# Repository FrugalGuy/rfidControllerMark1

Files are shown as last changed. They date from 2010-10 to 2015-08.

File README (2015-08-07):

This is the first incarnation of an Arduino-based RFID controller for an electric door strike.
This version does not do data logging or refer to an off-controller database for access control information.
Instead, RFID cards are registered directly at the reader.

  The sketch implements a controller for an RFID door lock system.
  It reads RFID cards and sends a signal to unlock a 
  door if the presented card is a valid card stored in EEPROM.
        
  The script currently can interface with HID card readers using Wiegand26
  protocol or with Innovations' ID-12 or ID-20 readers configured for 
  serial ASCII protocol.  The latter reads 125 KHz RFID cards / keyfobs.
   
  Additional features:
  1) System begins in 'factory default' mode. This is a 'virgin'
     state with no stored cards. When in this mode, lights flash in 
     a frenetic way. The first RFID card read after installation
     will become the 'master card' and factory default mode is exited.
     This little feature means you can burn tons of these chips and
     you don't need to hard-code any RFIDs. Suitable for shipping!
       
  2) Master card (first card read after installation) also opens
     the door, so you can just use that card for every day access
     instead of having to stash it somewhere.
        
  3) You can enter programming mode at any time with the Master card.
     To do this, you swipe the master card twice within a few seconds.
     First time opens the door, and second time (if door is still 
     unlocked) puts you in programming mode. You get sequential flashing 
     lights to indicate you are in programming mode.
    
  4) While in programming mode you can add any number of additional
     cards to the EEPROM. You can also remove any number of 
     cards from EEPROM while in this mode. You get a blinking green for
     adds and a blinking red for deletes. Previously unauthorized cards 
     will be added and authorized cards will be deleted. You exit 
     programming mode by swiping the master card again or after a period
     of inactivity.
			    
  5) Master card and other cards get a green/red light indicating
     pass/fail when trying to open the door.

  OPTIONAL FEATURES
  1) Master Swap option allows you to change the Master without
     resetting to factory default mode and erasing the additional
     cards. This is useful if you lose the Master card. Hold optional
     controller reset button for around 5 seconds.
  2) Device can be returned to factory default mode by pressing the 
     optional reset button for 15 seconds.
  3) Stealth option (not implemented) allows you to add your own RFID 
     card to the controller without having the Master card. Warning: Evil
			      
  DEVELOPMENT FEATURES
  1) Define a debug flag to get serial debug output.

  FUTURE POSSIBILITIES
  Data logging via wireless or HDSD card or enet/USB connector.
  Command line over serial to query and edit RFID database.
  IP web service interface for querying remote RFID db.
								      
  HARDWARE CONFIGURATIONS
  * Homegrown DIY using ID-12 or ID-20 RFID Reader
    I suggest two PCBs, one for the RFID reader and indicator lights 
    outside the door and a second for the controller inside. 
    Connect reader serial and light control lines to controller 
    located in a secure location (inside the access-controlled area). 
    Power for the door lock should be routed securely from the
    controller board to the door lock to prevent jumping. If you
    are providing a factory reset switch, some means of access to 
    the switch needs to be provided.
  * ProxPoint Plus Proximity Reader with Wiegand Output Model 6005
    For this you just need the interior controller connected to
    the reader outside the door, and power from the controller to
    the door lock.

  I've included Eagle files for the controller board and 
  Eagle files for the reader board for the ID-12/ID-20 chip
  configured for ASCII protocol.  You won't need the reader
  board if you're using a purchased HID Wiegand reader.

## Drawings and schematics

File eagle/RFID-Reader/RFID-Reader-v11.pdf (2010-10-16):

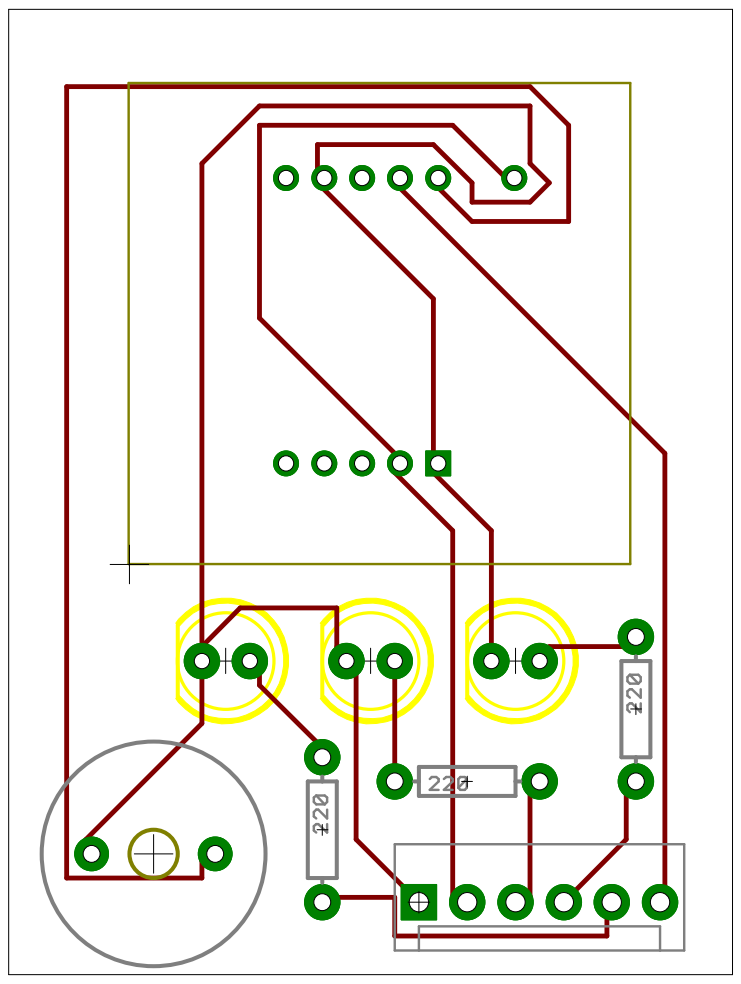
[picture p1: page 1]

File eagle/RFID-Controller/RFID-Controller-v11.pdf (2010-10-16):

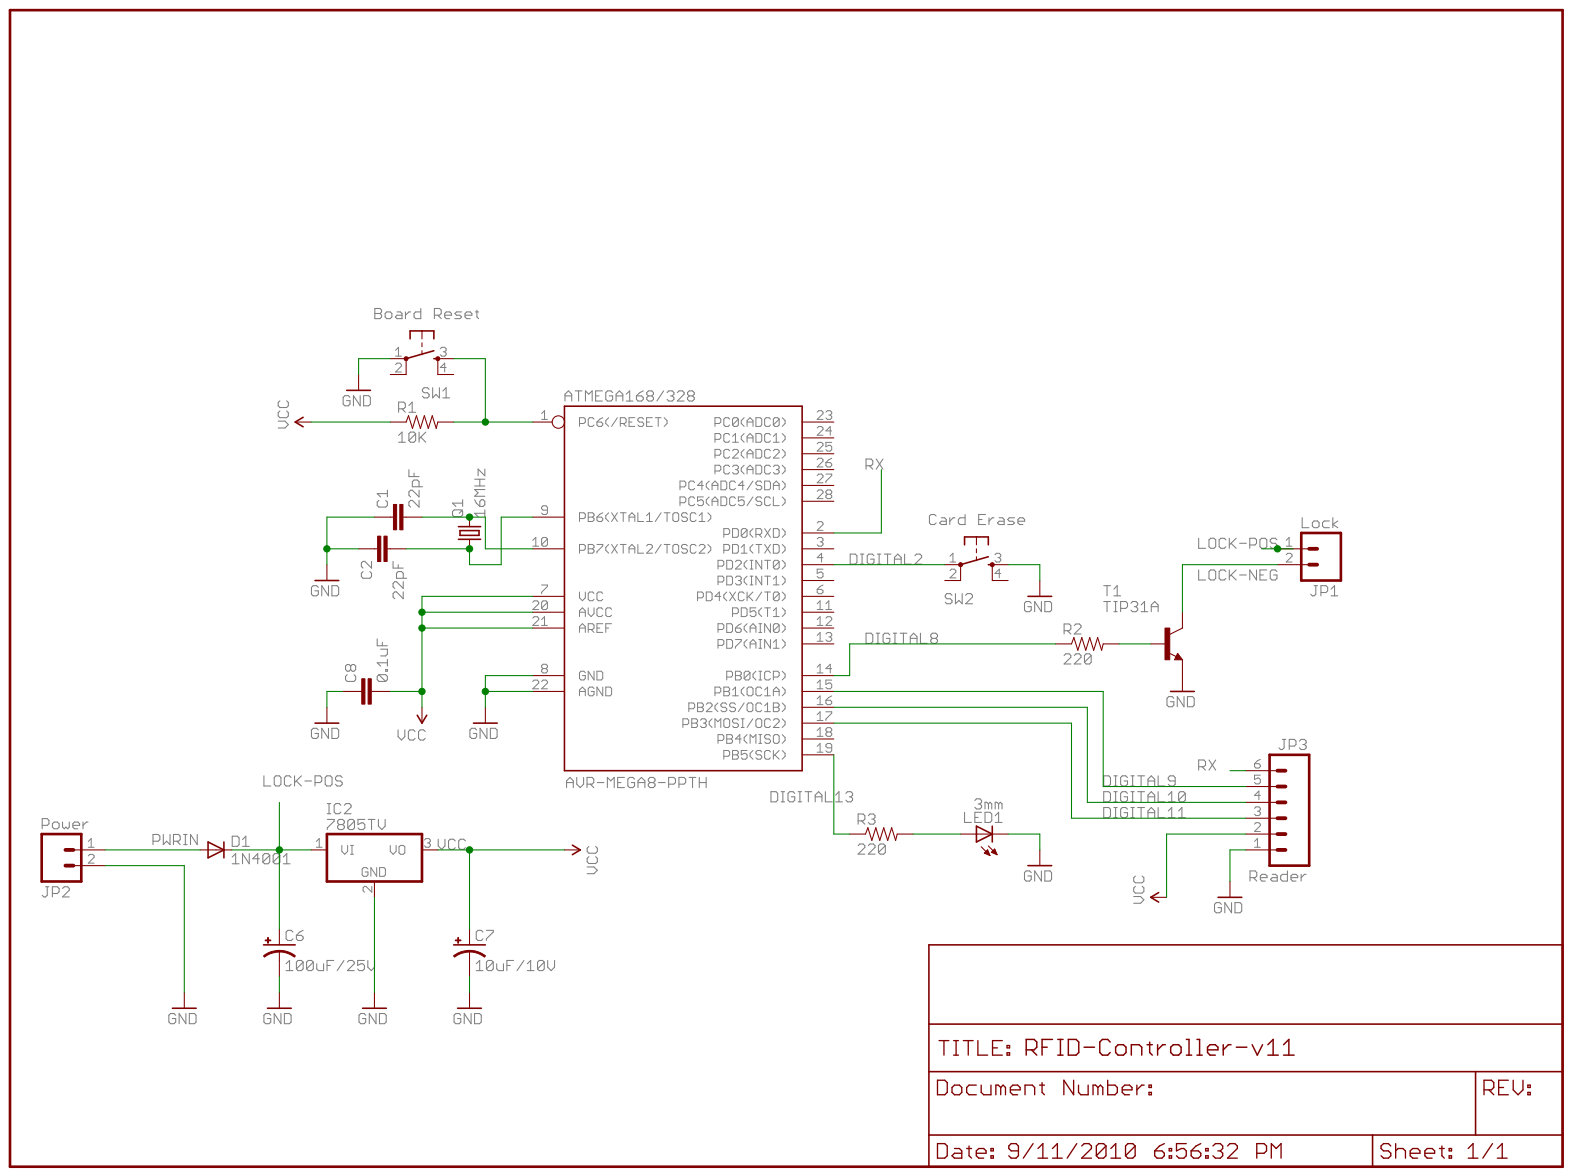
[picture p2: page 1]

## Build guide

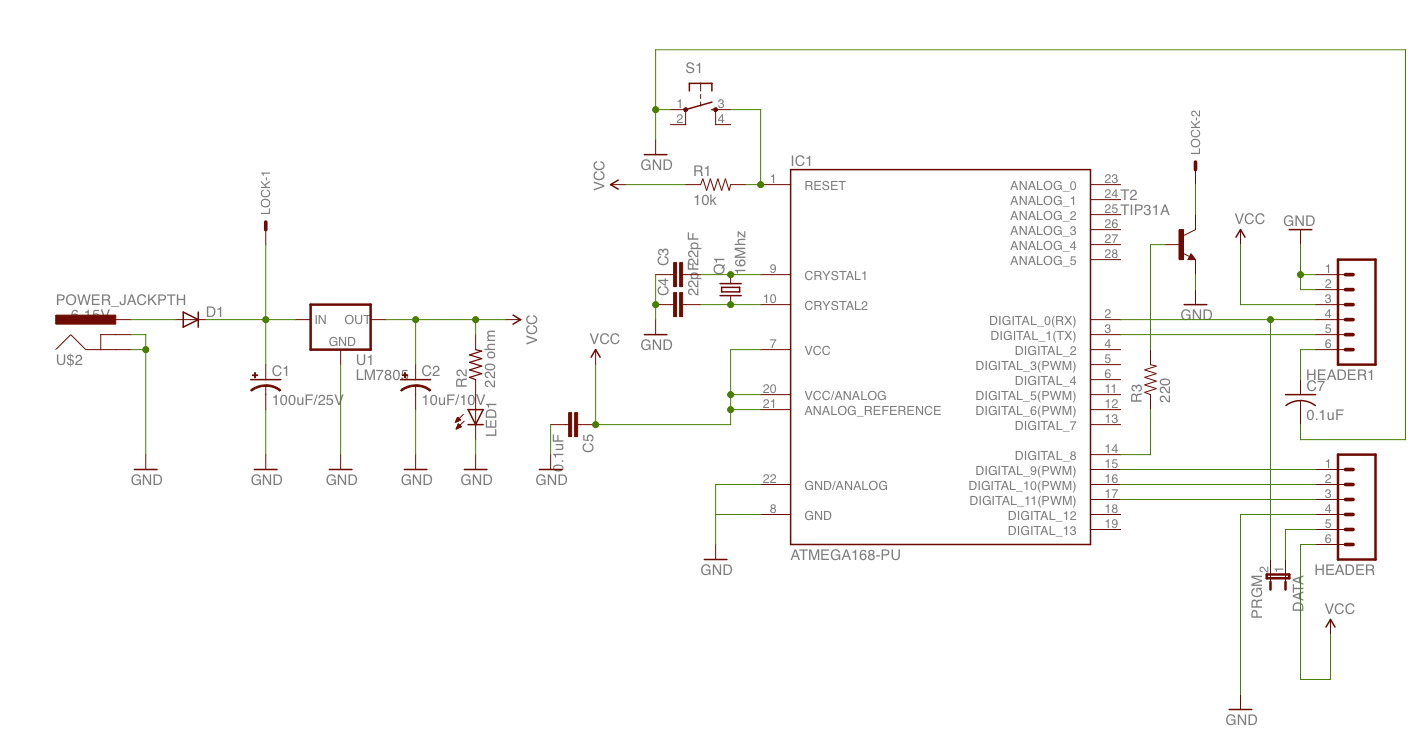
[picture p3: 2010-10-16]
eagle/RFID-Controller/Instructables-Schematic.png

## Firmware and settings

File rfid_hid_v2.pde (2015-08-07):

/*
  RFID Door Lock
  10APR2010, 17Oct2010
  Ron Craig
  roncraig007@gmail.com
  
  This sketch implements a controller for an RFID door lock system.
  It reads RFID cards and sends a signal to unlock a 
  door if the presented card is a valid card stored in EEPROM.
  
  The script currently can interface with HID card readers using Wiegand26
  protocol or with Innovations' ID-12 or ID-20 readers configured for 
  serial ASCII protocol.  The latter reads 125 KHz RFID cards / keyfobs.
  
  Additional features:
  1) System begins in 'factory default' mode. This is a 'virgin'
  state with no stored cards. When in this mode, lights flash in 
  a frenetic way. The first RFID card read after installation
  will become the 'master card' and factory default mode is exited.
  This little feature means you can burn tons of these chips and
  you don't need to hard-code any RFIDs. Suitable for shipping!
  
  2) Master card (first card read after installation) also opens
  the door, so you can just use that card for every day access
  instead of having to stash it somewhere.
  
  3) You can enter programming mode at any time with the Master card.
  To do this, you swipe the master card twice within a few seconds.
  First time opens the door, and second time (if door is still 
  unlocked) puts you in programming mode. You get sequential flashing 
  lights to indicate you are in programming mode.
  
  4) While in programming mode you can add any number of additional
  cards to the EEPROM. You can also remove any number of 
  cards from EEPROM while in this mode. You get a blinking green for
  adds and a blinking red for deletes. Previously unauthorized cards 
  will be added and authorized cards will be deleted. You exit 
  programming mode by swiping the master card again or after a period
  of inactivity.
  
  5) Master card and other cards get a green/red light indicating
  pass/fail when trying to open the door.
  
  OPTIONAL FEATURES
  1) Master Swap option allows you to change the Master without
  resetting to factory default mode and erasing the additional
  cards. This is useful if you lose the Master card. Hold optional
  controller reset button for around 5 seconds.
  2) Device can be returned to factory default mode by pressing the 
  optional reset button for 15 seconds.
  2) Stealth option (not implemented) allows you to add your own RFID 
  card to the controller without having the Master card. Warning: Evil
  
  DEVELOPMENT FEATURES
  1) Define a debug flag to get serial debug output.
  
  FUTURE POSSIBILITIES
  Data logging via wireless or HDSD card or enet/USB connector.
  Command line over serial to query and edit RFID database.
  IP web service interface for querying remote RFID db.
  
  HARDWARE CONFIGURATIONS
  * Homegrown DIY using ID-12 or ID-20 RFID Reader
  I suggest two PCBs, one for the RFID reader and indicator lights 
  outside the door and a second for the controller inside. 
  Connect reader serial and light control lines to controller 
  located in a secure location (inside the access-controlled area). 
  Power for the door lock should be routed securely from the
  controller board to the door lock to prevent jumping. If you
  are providing a factory reset switch, some means of access to 
  the switch needs to be provided.
  * ProxPoint Plus Proximity Reader with Wiegand Output Model 6005
  For this you just need the interior controller connected to
  the reader outside the door, and power from the controller to
  the door lock.

  
  COMPONENTS
  Mini SPST Push Button momentary reset switch (COM-00097 $0.35)
  
  ID-12/ID-20 RFID reader (SEN-08419 $29.95/SEN-08628 $34.95)

  Using www.sparkfun.com breakout board (SEN-08423 $0.95)
  [1] GND (Ground)
  [2] /RST (Reset Reader) Connect to +5V     
  [3] ANT (NC)  
  [4] ANT (NC)      
  [5] CP  (NC) (Card Present)     
  [6] NC
  [7] FS (Format select) (ground this for ASCII)
  [8] D1 (NC)
  [9] D0 (TTL Serial) to Arduino RX Pin
  [10] Buzzer/LED (Card read indicator) (Connect to transistor + buzzer/led to indicate card was read)
  [11] 5v+ ( +5vDC power) 

  On Arduino....
  [4] (Digital IN) to tactile push button reset switch connected to GND (optional)
  [13] (Digital OUT) to LED to indicate reset status (optional)
  [8] (Digital OUT) to lock relay+ 
  [9] (Digital OUT) to Red LED+ (fail/RFID erase indicator)
  [10] (Digital OUT) to Blue or Yellow LED+ (power indicator)
  [11] (Digital OUT) to Green LED+ (pass/RFID add indicator)
  [RX0] (Serial IN) to [9] D0 TTL serial out on ID-12/ID-20
    OR
  [2] (Digital IN) to Data0 on Wiegand26 reader
  [3] (Digital IN) to Data1 on Wiegand26 reader

// Expanded/modified from a version by Brett Martin www.pcmofo.com
// Based on code by BARRAGAN <http://people.interaction-ivrea.it/h.barragan> 
// and code from HC Gilje - http://hcgilje.wordpress.com/resources/rfid_id12_tagreader/
// Modified for Arudino by djmatic
// Modified for ID-12 and checksum by Martijn The - http://www.martijnthe.nl/
//
// Use the drawings from HC Gilje to wire up the ID-12/ID-20.
// Remark: disconnect the RX serial wire to the ID-12/ID-20 when uploading the sketch.


*/

// Debug settings. Define DEBUG to get serial output. Undefine otherwise.
#define DEBUG
//#undef DEBUG

// Define if your device speaks wiegand26. Undefine otherwise.
//#define wiegand
#undef wiegand


#include <EEPROM.h>

#ifdef wiegand
#include <WIEGAND26.h>   //Wiegand 26 reader format libary
#include <PCATTACH.h>    //Pcint.h implementation, allows for >2 software interupts.
#endif

// Version display. Visible with debug output
#define VERSION "RFID Controller V5 20101018 (c) Ron Craig 2010"

#ifdef DEBUG
#define DEBUGPRINT(...) {Serial.print(__VA_ARGS__);}
#define DEBUGPRINTLN(...) {Serial.println(__VA_ARGS__);}
#else
#define DEBUGPRINT(...) { }
#define DEBUGPRINTLN(...) { }
#endif

// outputs to reader board
#define failPin   9      // a red LED
#define powerPin 10      // a power LED
#define passPin  11      // a green LED

// Optional reset functions. Define RESET to get it. Undefine otherwise.
#define RESET
//#undef RESET
#ifdef RESET
#define resetPin  4      // optional factory reset 
#define resetLED 13      // optional reset indicator
#endif

#define doorPin   8      // signals door lock/relay

#define MAX_CARDS    100  // max cards to store in EEPROM (1 + IDSIZE*MAX_CARDS bytes required) ATmega168=512  328=1024

#define doorDelay   2500  // how long to keep door lock powered open (ms)
#define pgmDelay   30000  // how long to stay in programming mode without activity

#ifdef RESET
#define swapMin     5000  // how long you have to hold reset before you can read a new master card (ms)
#define factoryMin 15000  // how long you have to hold reset before entire EEPROM is cleared (ms)
#define resetDebounce 10  // prevent switch noise. Increase for noisy tactile switches.
#endif

boolean inited  = false;  // factory mode. If this is false, next card swiped becomes master card.
boolean pgmMode = false;  // programming mode
boolean pgmPend = false;  // programming mode pending (1 swipe)
unsigned long pModeTime = 0;     // programming mode timer
unsigned long doorTime  = 0;     // door open timer

#ifdef RESET
     unsigned long lastDebounceTime = 0;
     int buttonState     = HIGH;
     int lastButtonState = HIGH;  // default state of pin is HIGH
#endif

#define IDSIZE 5
byte storedCard[IDSIZE];      // card pulled from EEPROM
byte readCard[IDSIZE+1];      // card received from reader ([5] is checksum)
byte checksum = 0;       // independently calculated checksum

                   // overwritten from EEPROM during setup()
byte masterCard[IDSIZE] = {0xDE, 0xAD, 0xBE, 0xEF, 0xED};
byte cardCount = 0;

#ifdef wiegand
     byte reader1Pins[]={2,3};          // Reader 1 connected to pins 2 (data0), 3 (data1)

     // Enable door access reader.
     volatile long reader1 = 0;
     volatile int  reader1Count = 0;

     WIEGAND26 wiegand26;  // Wiegand26 (RFID reader serial protocol) library
     PCATTACH pcattach;    // Software interrupt library
#endif

void setup()
{
  Serial.begin(9600);
  DEBUGPRINTLN(VERSION)
  
  // Uncomment to set reader to Factory Settings on powerup. 
  // Alternatively, hold controller reset button for factoryMin milliseconds.
  // EEPROM.write(0,0);        // initializes to factory settings
  //
  
#ifdef wiegand
  // Attach pin change interrupt service routines from the Wiegand RFID reader
  pcattach.PCattachInterrupt(reader1Pins[0], callReader1Zero, CHANGE); 
  pcattach.PCattachInterrupt(reader1Pins[1], callReader1One,  CHANGE);  
  wiegand26.initReaderOne(); //Set up Reader 1 and clear buffers.
  delay(10);
  wiegand26.initReaderOne();
#endif
  
  pinMode(powerPin, OUTPUT);   // set LED pins and door pins for output
  pinMode(passPin,  OUTPUT);
  pinMode(failPin,  OUTPUT);
  pinMode(doorPin,  OUTPUT);

#ifdef RESET  
  // Optionally connect to reset switch to GND. If you don't it will stay high forever.
  pinMode(resetPin, INPUT);      // Chip has internal pullup resistor. http://www.arduino.cc/en/Tutorial/DigitalPins
  digitalWrite(resetPin, HIGH);  // This will hold level high until you ground it w/switch.
  pinMode(resetLED, OUTPUT);
  DEBUGPRINTLN("Reset feature included")
#endif
  
  inited = checkInit();       // also sets masterCard if known
  DEBUGPRINT("inited? ") DEBUGPRINTLN(inited, HEX)
}

boolean checkInit()
{
    int cnt = EEPROM.read(0);  // (0) holds number of known RFIDs
    if (cnt > 0) readMaster(); // initializes masterCard
    DEBUGPRINT(cnt, HEX)  DEBUGPRINTLN(" cards in EEPROM")
    DUMPEEPROM(1, (cnt*sizeof(storedCard)) );
    return (cnt > 0);
}


void loop()
{
  byte val = 0;

#ifdef RESET
  int reading = digitalRead(resetPin);   // Read the reset switch. If none installed, no problem.
  checkReset(reading); // if reset held long enough, clear master, maybe other cards, enter factory mode
#endif

  if (!inited)
  {
    factoryMode();  // will set inited and masterCard when a master card is stored
    return;         // skip all other processing while not inited
  }

  if (doorTime)
  {
    checkDoor();  //resets doorTime if expired
  }
  else if (pgmPend)
  {
    DEBUGPRINTLN("pgmPend-canceled")
    pgmPend = false;
  }

  if (pgmMode)
  {
    if ( (millis() - pModeTime) > pgmDelay )
    {
      DEBUGPRINTLN("pgmMode-exit")
      pgmMode = false; pModeTime = 0;
    }//pgmDelay expired
    else  // still in programming mode
    {
      pgmModeOn(); // cycle lights once
      if ( cardPresent() )
      {
          DEBUGPRINT("pgmMode.")
          getID();  // sets 'readCard' and 'checksum'
          pModeTime = millis(); // continue programming mode another 30 secs
          pgmPend = false;
          
          if ( ! isMasterCard(readCard) )
          {
            DEBUGPRINT("!Master.")
            if (int cardnum = findID(readCard) != -1)
            {
              DEBUGPRINTLN("known-eraseCard")
              eraseID(cardnum);
            }//known card
            else
            {
              DEBUGPRINTLN("unknown-addCard")
              addID(readCard);
            }//not known card
          }//not isMasterCard
          else
          {
            DEBUGPRINTLN("isMaster-quitPgm-openDoor")
            pgmMode = false;
            openDoor();
          }// isMasterCard
      }//cardPresent
    }//pgmDelay not expired
  }//pgmMode
  
  else  // not in programming mode
  {
    normalModeOn();  // adjust lights for normal operation
    if ( cardPresent() )
    {
        DEBUGPRINT("normal.")
        getID();  // sets 'readCard' and 'checksum'
        if ( readCard[5] == checksum )
        {
          DEBUGPRINT("goodChecksum.")
          if ( isMasterCard(readCard) )
          {
            DEBUGPRINT("isMaster.")
            if (pgmPend)
            {
              DEBUGPRINTLN("pgmMode")
              pgmMode = true; pModeTime = millis();
              pgmPend = false;
            }//pgmPend
            else
            {
              DEBUGPRINTLN("pgmPend-openDoor")
              openDoor();
              pgmPend = true;
            }//not pgmPend
          }//isMasterCard
          else
          {
            DEBUGPRINT("!Master.")
            pgmPend = false;  // read a non-master. cancel pending state
            if ( findID(readCard) != -1 )
            {
              DEBUGPRINTLN("known-openDoor")
              openDoor();
            }//known card
            else
            {
              DEBUGPRINTLN("unknown-failed")
              failed();
            }//not known card
          }//not isMasterCard
        }//checksum correct
        else 
        {
          DEBUGPRINTLN("bad-checksum")
        }
    }//cardPresent
  }//not pgmMode
} //loop

// changes lights, opens the door and starts a timer
// sets doorTime global variable
void openDoor()
{
  digitalWrite(powerPin, LOW);
  digitalWrite(failPin,  LOW);
  digitalWrite(passPin,  HIGH);
  digitalWrite(doorPin,  HIGH);
  doorTime = millis();
}//openDoor

// if the time for open door has elapsed, 
// then lock door, turn pass LED off, and reset timer doorTime
// otherwise, turn pass LED on
void checkDoor()
{
  if (millis() - doorTime > doorDelay)
  {
    DEBUGPRINTLN("closeDoor")
    digitalWrite(doorPin, LOW);
    digitalWrite(passPin, LOW);
    doorTime = 0;
  }//expired
  else
  {
    digitalWrite(passPin, HIGH); // likely was shut off elsewhere
  }//not expired
}//checkDoor

// cycle the LEDs once per call
// this delays 600 ms in all before returning
// called while in programming mode
void pgmModeOn()
{
  digitalWrite(powerPin, LOW);
  digitalWrite(failPin,  LOW);
  digitalWrite(passPin,  HIGH);
  delay(200);
  digitalWrite(passPin,  LOW);
  digitalWrite(powerPin, LOW);
  digitalWrite(failPin,  HIGH);
  delay(200);
  digitalWrite(failPin,  LOW);
  digitalWrite(passPin,  LOW);
  digitalWrite(powerPin, HIGH);
  delay(200);
}//pgmModeOn

// read the RFID from the reader
// sets readCard and checksum
#ifdef wiegand
void getID()
{
  long r = reader1;
  checksum = 0;
  readCard[0] = 0;
  readCard[1] = (byte)r >> 24 & 0xff;
  readCard[2] = (byte)r >> 16 & 0xff;
  readCard[3] = (byte)r >>  8 & 0xff;
  readCard[4] = (byte)r       & 0xff;
  readCard[5] = checksum;
#ifdef DEBUG
  Serial.print("RFID Read:");
  for (int i = 0; i < sizeof(readCard); i++)
  {
    Serial.print(" ");
    Serial.print(readCard[i], HEX);
  }
  Serial.println();
#endif
}
#else
void getID()
{
  byte cnt = 0;
  byte i = 0;
  byte val = 0;
  byte temp = 0;
  checksum = 0;    // reset with each call
  while ( cnt < 12 )
  {
    if (Serial.available() > 0)
    {
      val = Serial.read();
      if ( (val == 0x0D) || (val == 0x0A) || (val == 0x03) || (val == 0x02) )
        break;
      if ( (val >= '0') && (val <= '9') )
        val = val - '0';
      else if ( (val >= 'A') && (val <= 'F') )
        val = 10 + (val - 'A');
      
      if (cnt & 1 == 1)
      {
        readCard[cnt >> 1] = (val | (temp << 4) );
        if (cnt >> 1 != 5)
        {
          checksum ^= readCard[cnt >> 1];
        }//not done
      }//full byte read
      else
      {
        temp = val;
      }//not full byte read
      cnt++;        
    }//Serial.available
  }//while
}//getID
#endif

// return boolean telling if supplied IDs are the same
// a possible 6th byte is ignored--it is a checksum
boolean areEqual(byte a[], byte b[])
{
  for (int i = 0; i < IDSIZE; i++)
  {
    if (a[i] != b[i]) return false; // return truth. breaks for loop
  }//for
  return true;
}//areEqual

// return boolean telling if supplied card is the master card
boolean isMasterCard(byte m[])
{
  if ( areEqual(m, masterCard) )
    return true;
  return false;
}//isMasterCard

// set storedCard to the ID in given EEPROM card slot, counts from 1
void readID(int num)
{
  int start = (num * IDSIZE) - (IDSIZE-1);
  for (int j = 0; j < IDSIZE; j++)
  {
    storedCard[j] = EEPROM.read(start + j);
  }//for
}//readID

// returns index of supplied ID if in EEPROM
// otherwise returns -1
int findID(byte f[])
{
  int cnt = EEPROM.read(0); // (0) holds number of active cards
  for (int i = 1; i <= cnt; i++)
  {
    readID(i);  // sets storedCard
    if ( areEqual(f, storedCard) )
      return i;  // return index. breaks for loop
  }//for
  return -1;     // return failure. did entire loop w/out success
}//findID

// erase an ID from EEPROM, given its 1-based position
void eraseID(int i)
{
  if (i < 1) return;
  int cnt = EEPROM.read(0); // (0) holds number of active cards
  if (i > cnt) return;
  if (i < cnt)
  {
    int start = (cnt * IDSIZE) - (IDSIZE-1);
    int finish= (cnt - 1) * IDSIZE;
    byte val;
    for ( ; start <= finish; start++)
    {
      val = EEPROM.read(start + IDSIZE);
      EEPROM.write(start, val);
    }//for
  }//i < cnt
  EEPROM.write(0, --cnt); // if i==cnt just reduce the count
  failedWrite();
}//eraseID

// add the supplied ID to the EEPROM. increase count of cards
// blinks lights to indicate success or failure
void addID(byte a[])
{
  int cnt = EEPROM.read(0); // (0) holds number of active cards
  if ( (cnt < MAX_CARDS) &&
       (-1 == findID(a)) )
  {
    int start = (cnt * IDSIZE) + 1;
    for (int j = 0; j < IDSIZE; j++)
    {
      EEPROM.write( start + j, a[j] );
    }//for
    EEPROM.write(0, ++cnt);
    successWrite();        // blink success lights
  }//new card and room
  else
  {
    failedWrite();         // blink failure lights
  }//not new card or not room
}//addID

// set LEDs for normal operation
void normalModeOn()
{
  digitalWrite(failPin,  LOW);
  //digitalWrite(passPin,  LOW); puts door open indicator at half-bright
  digitalWrite(powerPin, HIGH);
}//normalModeOn

// flash failure LED
// this delays 2,500 ms before returning!!
void failed()
{
  digitalWrite(passPin,  LOW);
  digitalWrite(powerPin, LOW);
  digitalWrite(failPin, HIGH);
  delay(500);
  digitalWrite(failPin, LOW);
  delay(500);
  digitalWrite(failPin, HIGH);
  delay(500);
  digitalWrite(failPin, LOW);
  delay(500);
  digitalWrite(failPin, HIGH);
  delay(500);
  digitalWrite(failPin, LOW);
}//failed

// flash successful write LEDs
// delays 1000 ms before returning!
void successWrite()
{
  digitalWrite(failPin,  LOW);
  digitalWrite(powerPin, LOW);
  digitalWrite(passPin, HIGH);
  delay(200);
  digitalWrite(passPin, LOW);
  delay(200);
  digitalWrite(passPin, HIGH);
  delay(200);
  digitalWrite(passPin, LOW);
  delay(200);
  digitalWrite(passPin, HIGH);
  delay(200);
}//successWrite

// flash failed write LEDs
// delays 1000 ms before returning!
void failedWrite()
{
  digitalWrite(passPin,  LOW);
  digitalWrite(powerPin, LOW);
  
  digitalWrite(failPin, HIGH);
  delay(200);
  digitalWrite(failPin, LOW);
  delay(200);
  digitalWrite(failPin, HIGH);
  delay(200);
  digitalWrite(failPin, LOW);
  delay(200);
  digitalWrite(failPin, HIGH);
  delay(200);
}//successWrite

// called each loop while not inited
// records next RFID read as the master
// and sets the state to inited
void factoryMode()
{
    byte val;
    flashFactory();  
    if ( cardPresent() )
    {
            getID();                          // sets 'readCard' and 'checksum'
            if (readCard[5] == checksum)
            {
                DEBUGPRINTLN("factoryMode.cardRead")
                writeMaster(readCard); // sets 'masterCard', optional erases all others
                if ( findID(readCard) == 1 )
                {
                    inited = true;
                    DEBUGPRINTLN("factoryMode-exit")
                }
            }
    }
}//factoryMode

// reads first card from EEPROM into masterCard
void readMaster()
{
    for (int i = 0; i < IDSIZE; i++)
    {
        masterCard[i] = EEPROM.read( i+1 );
    }
}//readMaster

// sets masterCard and first card slot in EEPROM to supplied value
// if there are no other cards (factory mode), marks new master as the only card
// otherwise does not disturb the card count, so you could replace the master card
void writeMaster(byte m[])
{
    for (int i = 0; i < IDSIZE; i++)
    {
        EEPROM.write( i+1, m[i] );
        masterCard[i] = m[i];
    }
    DEBUGPRINTLN("writeMaster.RfidWritten")
    if ((EEPROM.read(0) <= 0)) {
       EEPROM.write( 0, 1 );
       DEBUGPRINTLN("writeMaster.cardCountNow1")
    }
#ifdef RESET    
    digitalWrite(resetLED, LOW);
#endif
}//writeMaster

// this delays 500 ms before returning
// it flashes the lights to indicate the reader is in factory mode
void flashFactory()
{
    digitalWrite(powerPin, HIGH);
    digitalWrite(passPin,  LOW);
    digitalWrite(failPin,  LOW);
    delay(100);
    digitalWrite(powerPin, LOW);
    delay(100);
    digitalWrite(powerPin, HIGH);
    digitalWrite(passPin,  HIGH);
    digitalWrite(failPin,  HIGH);
    delay(100);
    digitalWrite(powerPin, LOW);
    delay(100);
    digitalWrite(powerPin, HIGH);
    digitalWrite(passPin,  LOW);
    digitalWrite(failPin,  LOW);
    delay(100);
}//flashFactory
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

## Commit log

2010-10-16 adding Controller eagle files for board layout and schematic
    [RFID-Controller-v10.brd, RFID-Controller-v10.sch, RFID-Controller-v11.brd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]
2010-10-16 adding Reader eagle files
    [RFID-Reader-v10.brd, RFID-Reader-v10.sch, RFID-Reader-v11.brd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]
2010-10-16 adding v4 of Arduino code
